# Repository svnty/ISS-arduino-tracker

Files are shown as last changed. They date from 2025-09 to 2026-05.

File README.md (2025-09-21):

<p align="center">
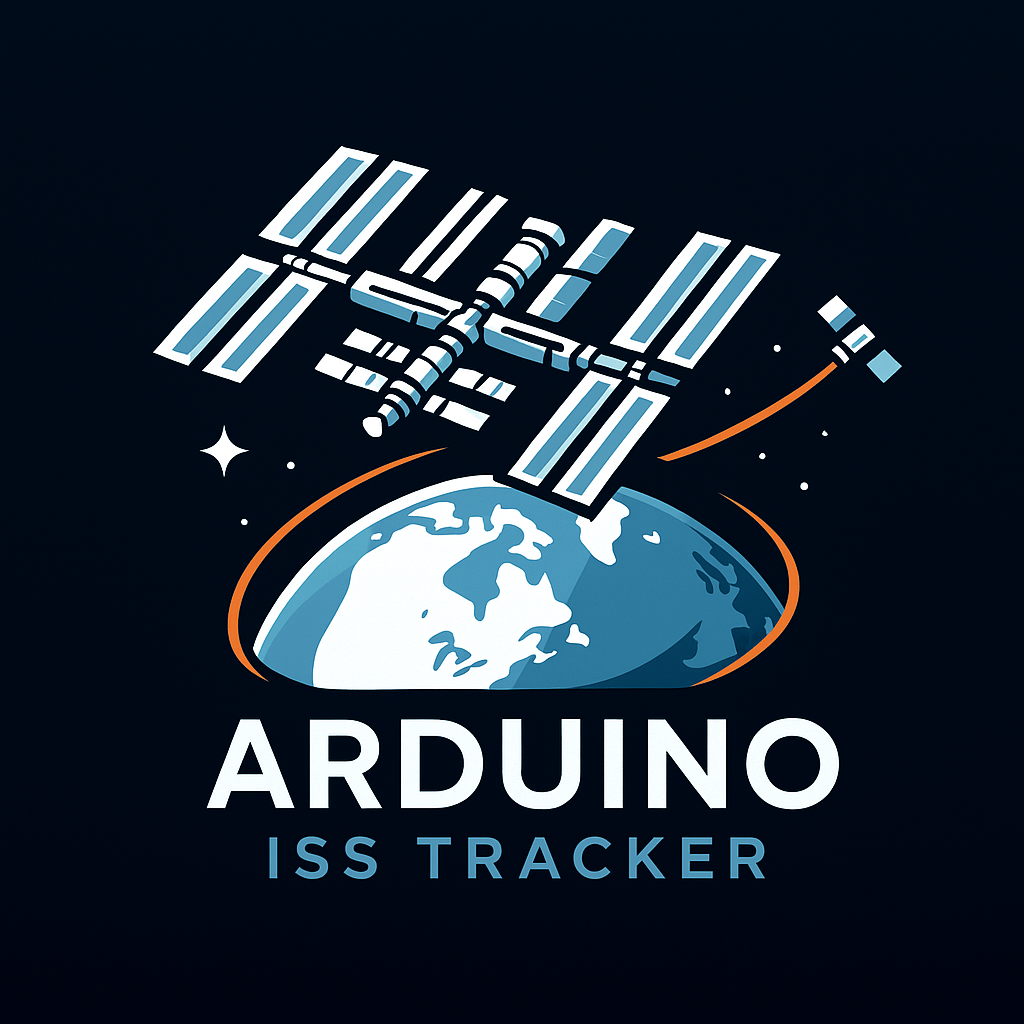
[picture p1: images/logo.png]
  
</p>

# International Space Station Orbit Tracker

Arduino implementation of an ISS tracker

Print all files in stl_files folder, use Nylon for the bearing (Race Inner Bottom, Race Inner Top, Race Outer, Rolls) at a high infill, and PLA for everything else at 15% infill.

## Model

<p align="center">
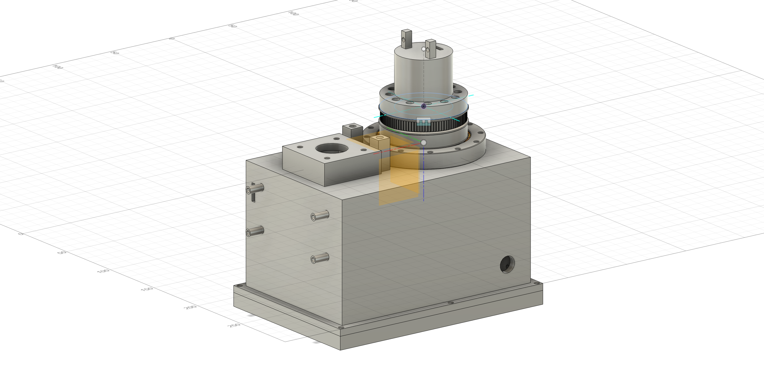
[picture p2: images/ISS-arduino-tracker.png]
International Space Station Orbit Tracker
  
</p>

## Parts list

| Part | Cost (AUD) |
|--|--|
| [Ardino uno R4 WiFi](https://www.jaycar.com.au/arduino-uno-wifi-r4-development-board/p/XC9211) | $50 |
| [Nema 17 stepper motor](https://www.jaycar.com.au/nema17-stepper-motor/p/YM2756) | $25 |
| [SG90 servo motor](https://www.jaycar.com.au/arduino-compatible-9g-micro-servo-motor/p/YM2758) | $12 |
| [TMC2209 stepper motor driver](https://www.ebay.com.au/sch/i.html?_nkw=TMC2209) | $15 |
| [230V AC -> 12V DC power supply](https://www.jaycar.com.au/mean-well-35w-12v-3a-power-supply/p/MP3285) | $40 |
| [12V DC -> 9V DC voltage regulator](https://core-electronics.com.au/20w-adjustable-dc-dc-buck-converter-with-digital-display.html) | $10 |
| [GY-271 QMC5883 magnometer](https://www.ebay.com.au/sch/i.html?_nkw=QMC5883+GY-271) | $5 |
| [12 wire 5A slip ring 22mm](https://www.ebay.com.au/sch/i.html?_nkw=22mm+12+wire+5A+slip+ring) | $30 |
| 15 AWG wire | $5 |
| 20 AWG wire | $15 |
| Dupont jumper wires | $20 |
| 16x2 LCD + i2c Backpack | $10 |
| 1kg Nylon filament | $60 |
| 1kg PLA filament | $20 |
| [ATGM336H GPS](https://www.ebay.com.au/sch/i.html?_nkw=BDS+GPS+ATGM336H) | $20 |
| Solder breadboard | $15 |
| 3 pin rocker power switch | $10 |
| M3 nuts + screws | $10 |
| PTFE grease | $10 |
| Solder | $5 |
| Heat shrink | $5 |
| Electrical tape | $5 |
| 1m GT2 pulley belt | $10 |
| Superglue | $1 |
| 2.1mm DC barrel jack | $2 |
| Contact Cement | $10 |
| 100 uF capacitor | $2 |

Total cost: ≈ $400

## Tools used

1. Anycubic Kobra S1 3D printer
2. TS80 soldering iron
3. Phillips head screwdriver
4. Precision knife

# Build Example

<p align="center">
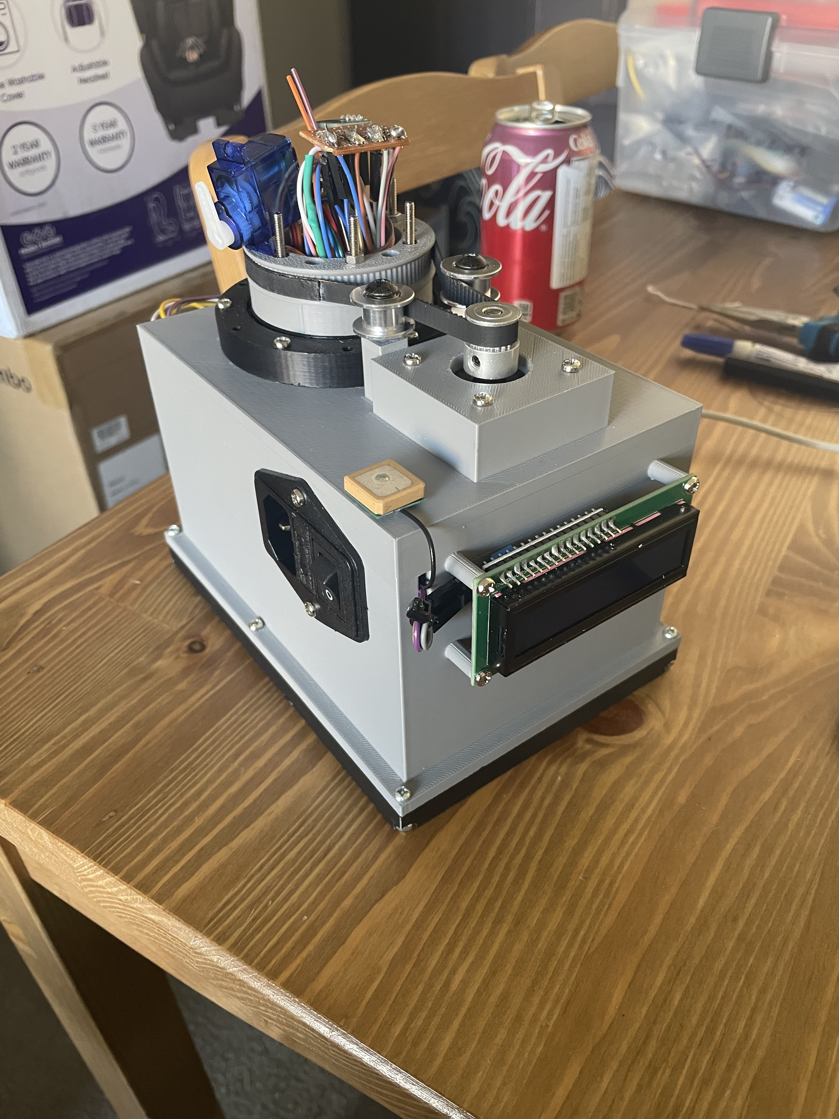
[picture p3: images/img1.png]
  
</p>

<p align="center">
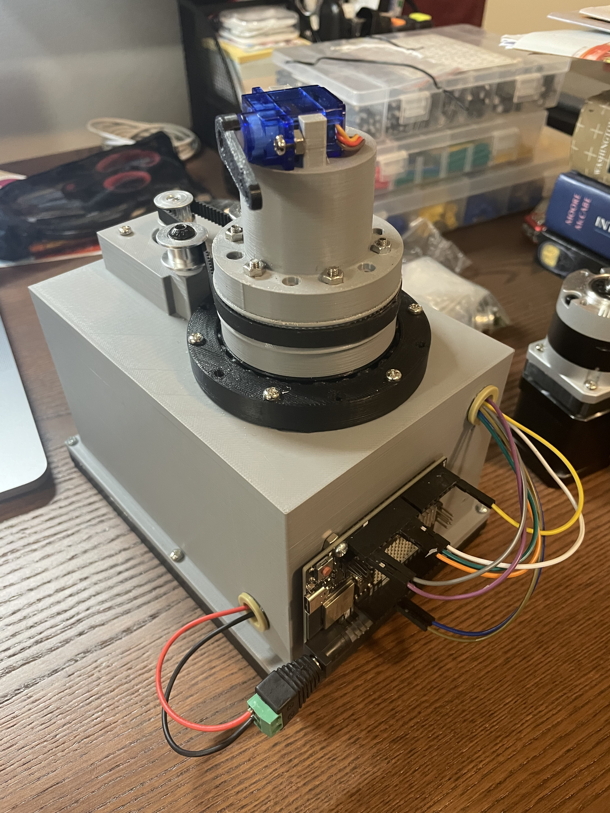
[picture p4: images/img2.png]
  
</p>

# Credits

Inspired by 
[Grady Hillhouse's ISS tracking pointer](https://github.com/gradyh/ISS-Tracking-Pointer/tree/master), as seen on [Youtube](https://www.youtube.com/watch?v=sIE0mcOGnms).

# Troubleshooting

Can't open the project? Open it in VS-Code and install the `svnty.vscode-arduino-intellisense` VS-Code extension.

# Power usage

Device uses 12W (aprox 0.23A).

# TODO

- Add 3S LiPo support?

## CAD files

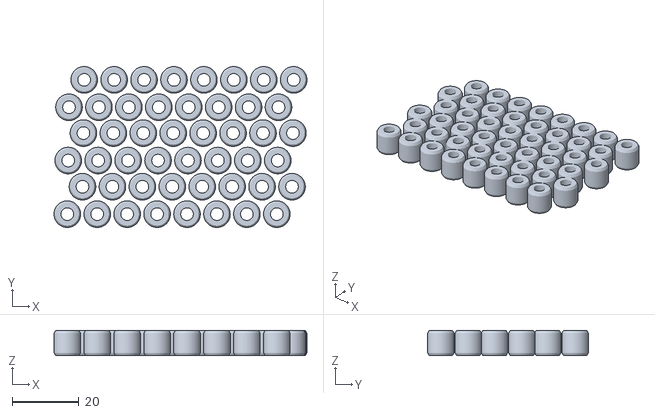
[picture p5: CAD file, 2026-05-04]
3d-models/stl_files/Rolls.stl
76.1 x 48.4 x 7.60

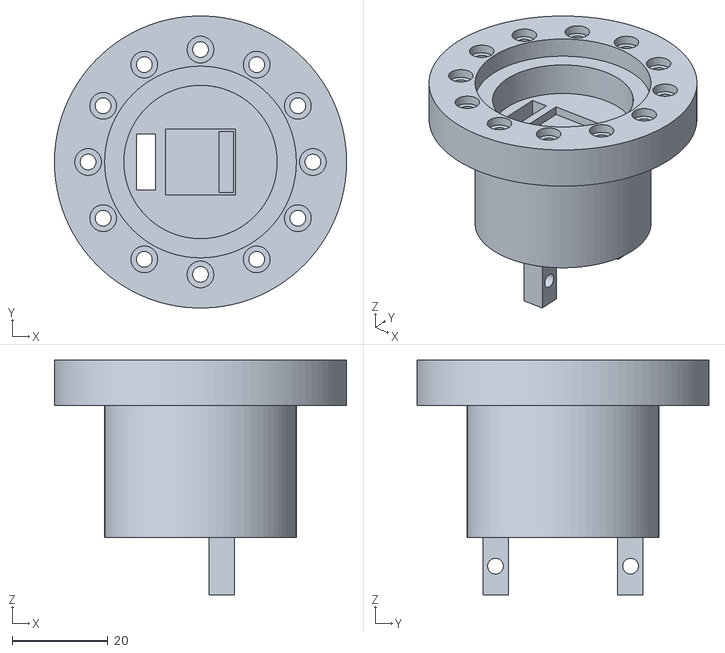
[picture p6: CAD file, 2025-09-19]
3d-models/stl_files/Top.stl
61.0 x 60.9 x 49.0

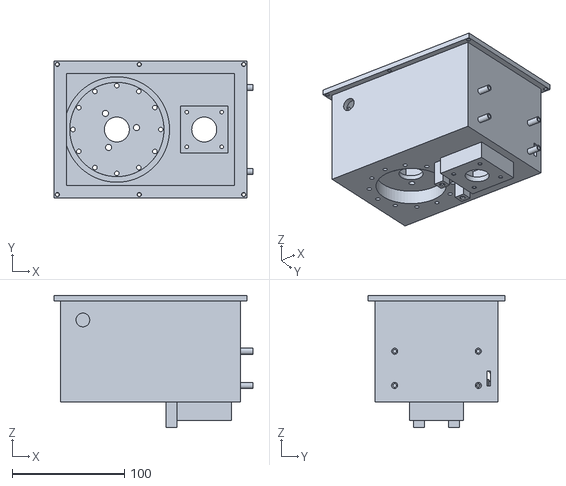
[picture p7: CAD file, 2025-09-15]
3d-models/stl_files/Housing.stl
177.3 x 122.0 x 117.8

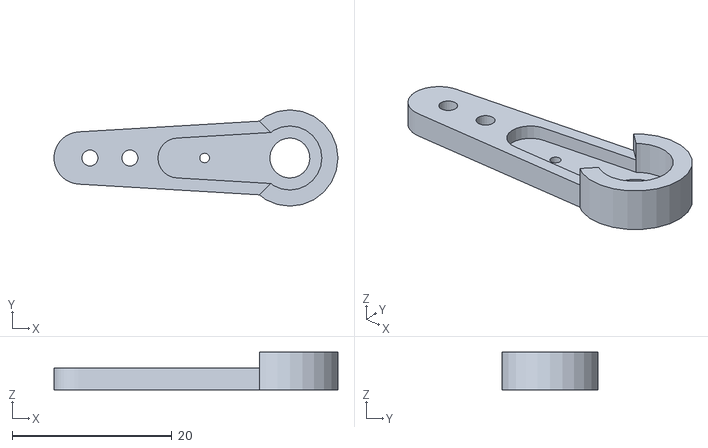
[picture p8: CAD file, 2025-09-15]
3d-models/stl_files/Servo-Extender.stl
35.5 x 12.0 x 4.70

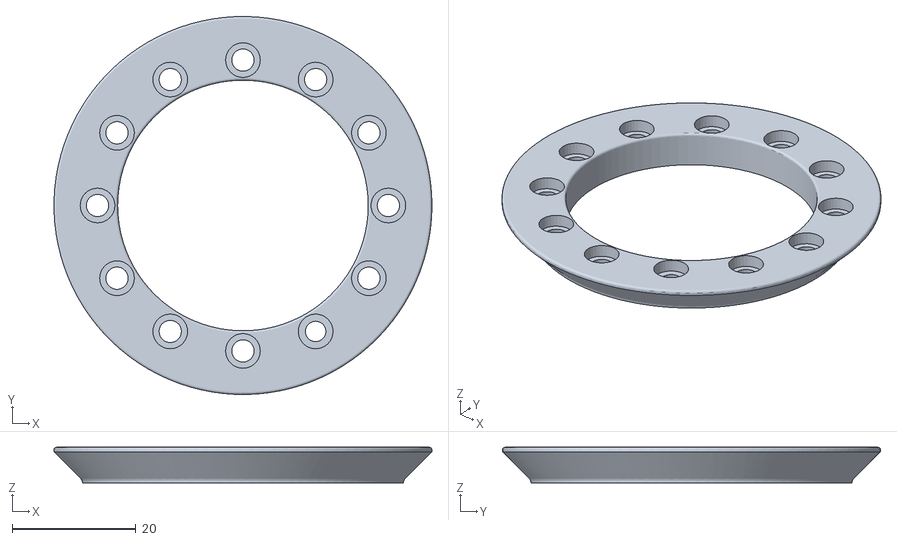
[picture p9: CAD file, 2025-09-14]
3d-models/stl_files/Race Inner Top.stl
61.0 x 61.0 x 5.73

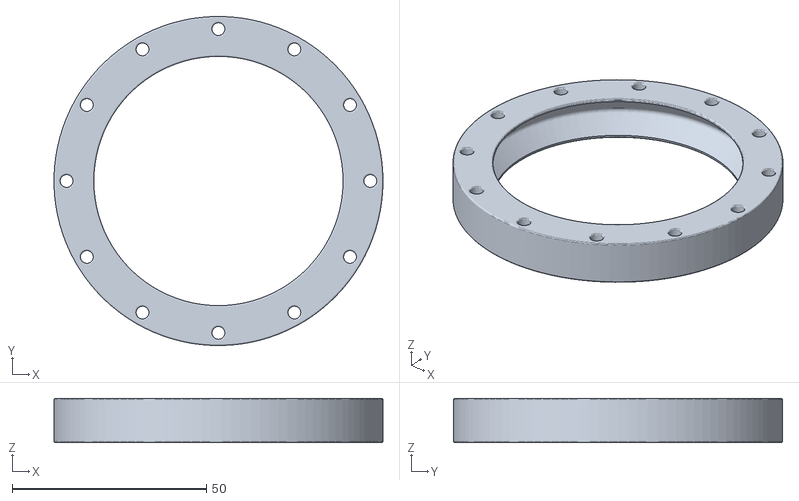
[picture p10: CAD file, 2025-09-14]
3d-models/stl_files/Race Outer.stl
84.7 x 84.7 x 11.5

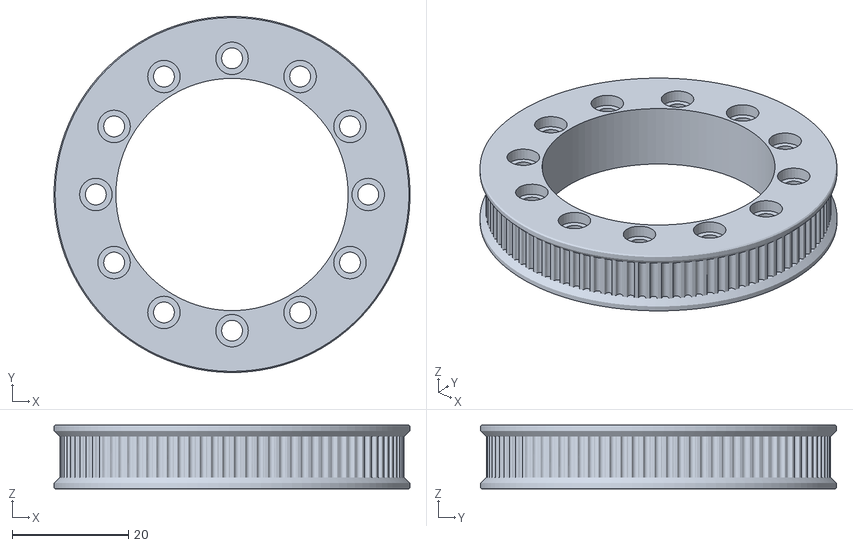
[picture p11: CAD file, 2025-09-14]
3d-models/stl_files/Pulley.stl
61.3 x 61.3 x 11.0

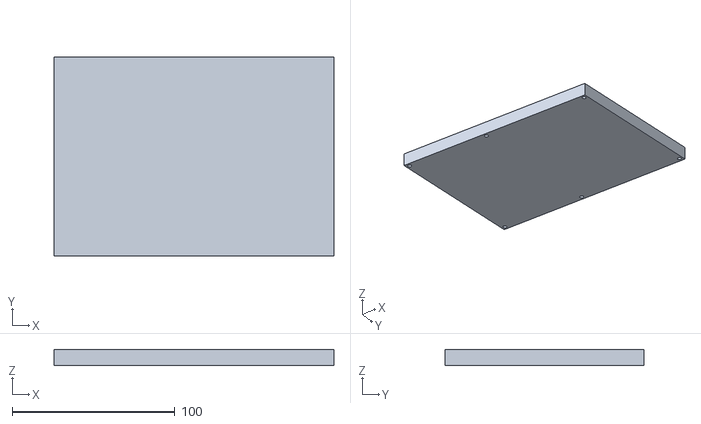
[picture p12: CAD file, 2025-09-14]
3d-models/stl_files/Base.stl
172.0 x 122.0 x 10.0

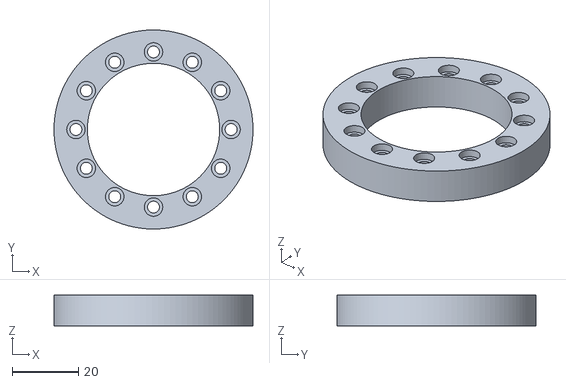
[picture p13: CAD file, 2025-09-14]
3d-models/stl_files/Spacer.stl
60.2 x 60.2 x 9.30

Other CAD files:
3d-models/stl_files/Race Inner Bottom.stl
3d-models/fusion-360/ISS-arduino-tracker.f3d

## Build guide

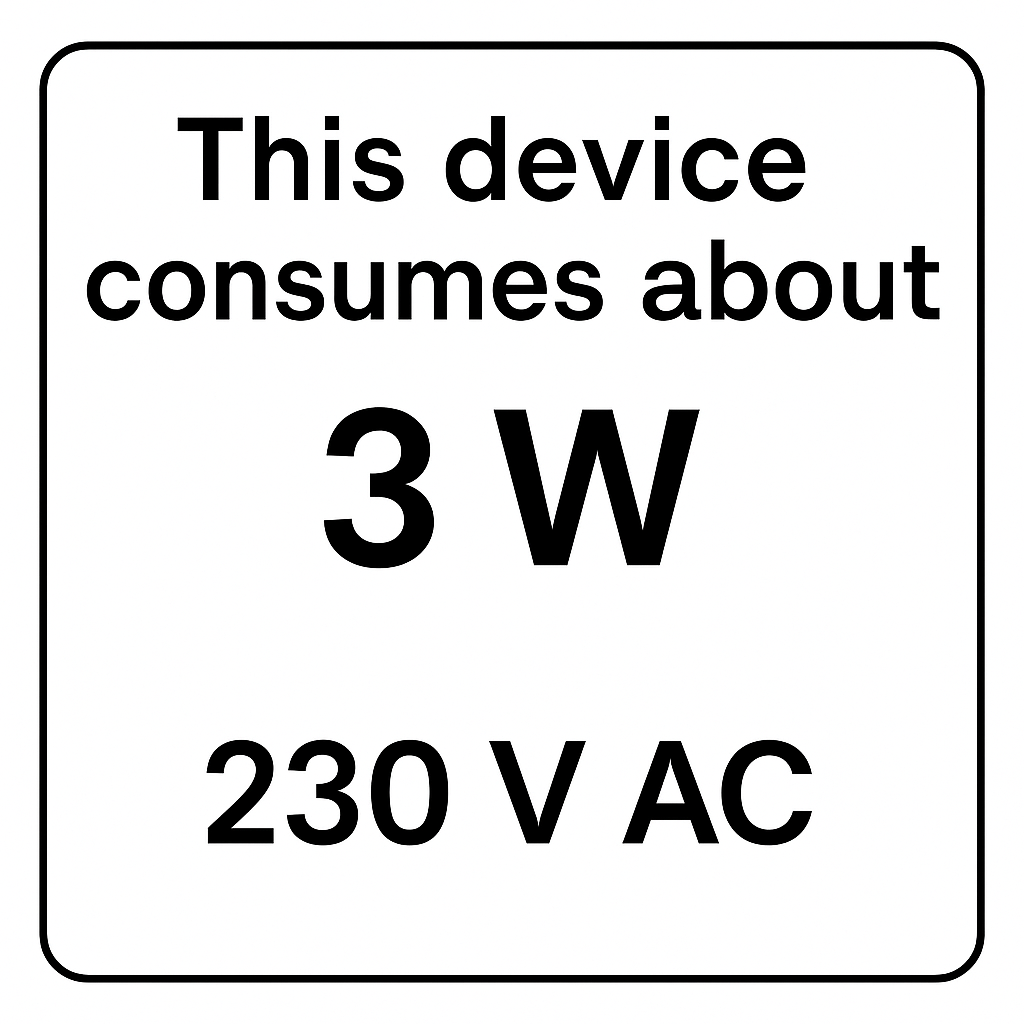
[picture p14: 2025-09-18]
images/power-usage.png

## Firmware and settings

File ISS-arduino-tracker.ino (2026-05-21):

/**
 * International Space Station (ISS) orbit tracker
 * Tracks the ISS using TLE data from Celestrak, observer location from GPS,
 * magnetic declination from NOAA, and points a motorized antenna mount
 * towards the ISS.
 *
 * @author svnty (Jake Walklate)
 * @date September 2025
 * @copyright © 2025 Jake Walklate
 */

#include <Arduino.h>
#include <ArduinoJson.h>
#include <LiquidCrystal_I2C.h>
#include <QMC5883LCompass.h>
#include <Servo.h>
#include <TinyGPSPlus.h>
#include <WiFiS3.h>
#include <Wire.h>
#include <math.h>

#include "SGP4_vallado/sgp4coord.cpp"
#include "SGP4_vallado/sgp4coord.h"
#include "SGP4_vallado/sgp4ext.cpp"
#include "SGP4_vallado/sgp4ext.h"
#include "SGP4_vallado/sgp4unit.cpp"
#include "SGP4_vallado/sgp4unit.h"

// -------- SYSTEM TOGGLES --------
static const bool ENABLE_WIFI = true;
static const bool ENABLE_LOG = true;
static const bool ENABLE_GPS = true;

// -------- CONSTANTS --------
// pins
static const uint8_t ELEVATION_PIN = 9;
static const uint8_t AZIMUTH_DIR_PIN = 10;
static const uint8_t AZIMUTH_STEP_PIN = 11;
static const uint8_t GPS_RX_PIN = 12;
// stepper motor
static const float TMC2209_RESISTANCE = 0.11;  // ohms
// wifi
static const char *WIFI_SSID = "Jakes iPhone", *WIFI_PASSWORD = "izeh5zemxa05r";
// http
static const char *DECLINATION_HOST = "www.ngdc.noaa.gov";
static const char *DECLINATION_API_KEY = "zNEw7";
static const char *TLE_API_HOST = "celestrak.org";
static const uint16_t PORT = 443;
// i2c
static const uint8_t MAX_i2c_DEVICES = 16;
// compass
static const float COMPASS_AZIMUTH_OFFSET = 17.0;               // degrees
static const float COMPASS_JUMP_THRESHOLD = 5.0;               // degrees
static const unsigned long COMPASS_CHECK_INTERVAL = 5 * 1000;  // 5 seconds
// lcd
static const unsigned long LCD_UPDATE_INTERVAL = 5 * 1000;  // 5 seconds
// wifi
static const unsigned long WIFI_UPDATE_INTERVAL = 60 * 60 * 1000 + 60 * 30 * 1000;  // 1 hour + 30 minutes
static const unsigned long WIFI_TIMEOUT_TIME = 60 * 1000;          // 1 minute
// gps
static const unsigned long GPS_UPDATE_INTERVAL = 10 * 60 * 1000;  // 10 minutes
static const unsigned long GPS_TIMEOUT_INTERVAL = 60 * 1000;      // 1 minute

// -------- VARIABLES --------
// timers
static unsigned long lastLcdUpdateTime = 0;
static unsigned long lastLcdResetTime = 0;
static unsigned long lastGpsUpdateTime = 0;
static unsigned long lastWiFiUpdateTime = 0;
static unsigned long lastWiFiReconnectAttemptTime = 0;
static unsigned long gpsTimeoutTimer = 0;
static unsigned long lastTimeUpdateMillis = 0;
// http data
static bool foundISSbyWifi = false;
static uint8_t findISSbyWifiAttempts = 0;
static bool foundDeclinationByWifi = false;
static uint8_t findDeclinationByWifiAttempts = 0;
static float magneticDeclination = 12.7;  // degrees
static char tle_line1[70];
static char tle_line2[70];
// gps data
static double observerLatitude = 0.0, observerLongitude = 0.0, observerAltitude = 0.0;
static int year, month, day, hour, minute, second;
static bool isGpsFixed = false;
static uint32_t gpsDateAge = 0;
static uint32_t gpsLocationAge = 0;
// motor control
static float currentAzimuth = 0.0;
static float currentElevation = 95.0;
// compass
static float previousCompassHeading = 0.0;
static unsigned long lastCompassCheckTime = 0;
static unsigned long compassLastCalibrate = 0;
static float compassOffsetX = 0.0, compassOffsetY = 0.0, compassOffsetZ = 0.0;
static float compassScaleX = 1.0, compassScaleY = 1.0, compassScaleZ = 1.0;
// i2c
static uint8_t i2cDeviceAddresses[MAX_i2c_DEVICES];
static uint8_t i2cDeviceCount = 0;
// lcd
static unsigned long lcdDisplayMode = 0;

// -------- SERIALS --------
HardwareSerial &GPS_SERIAL = Serial1;

// -------- OBJECTS --------
TinyGPSPlus gps;
LiquidCrystal_I2C lcd(0x27, 16, 2);
QMC5883LCompass compass;
elsetrec satrec;
Servo elevation;

// -------- FUNCTIONS --------
void calibrateCompass() {
  int minX = 32767, maxX = -32768;
  int minY = 32767, maxY = -32768;
  int minZ = 32767, maxZ = -32768;

  Serial.println("Starting QMC5883L calibration. Please rotate the sensor in all directions for 20 seconds.");
  unsigned long startTime = millis();
  while (millis() - startTime < 20 * 1000) {
    compass.read();

    int x = compass.getX();
    int y = compass.getY();
    int z = compass.getZ();
    minX = min(minX, x); maxX = max(maxX, x);
    minY = min(minY, y); maxY = max(maxY, y);
    minZ = min(minZ, z); maxZ = max(maxZ, z);

    digitalWrite(AZIMUTH_STEP_PIN, HIGH);
    delayMicroseconds(1000);
    digitalWrite(AZIMUTH_STEP_PIN, LOW);
    delayMicroseconds(1000);
  }

  compassOffsetX = (maxX + minX) / 2.0;
  compassOffsetY = (maxY + minY) / 2.0;
  compassOffsetZ = (maxZ + minZ) / 2.0;
  compassScaleX = (maxX - minX) / 2.0;
  compassScaleY = (maxY - minY) / 2.0;
  compassScaleZ = (maxZ - minZ) / 2.0;

  Serial.println("Compass calibration complete.");
  Serial.print("Offset X: "); Serial.println(compassOffsetX);
  Serial.print("Offset Y: "); Serial.println(compassOffsetY);
  Serial.print("Offset Z: "); Serial.println(compassOffsetZ);
  Serial.print("Scale X: "); Serial.println(compassScaleX);
  Serial.print("Scale Y: "); Serial.println(compassScaleY);
  Serial.print("Scale Z: "); Serial.println(compassScaleZ);
  lcdSetSecondLine("OK");
}

void lcdClear() {
  lcd.setCursor(0, 0);
  lcd.print("                ");
  lcd.setCursor(0, 1);
  lcd.print("                ");
}

void lcdSetFirstLine(String firstLineText) {
  lcd.setCursor(0, 0);
  lcd.print("                ");
  lcd.setCursor(0, 0);
  lcd.print(firstLineText);
}

void lcdSetSecondLine(String secondLineText) {
  lcd.setCursor(0, 1);
  lcd.print("                ");
  lcd.setCursor(0, 1);
  lcd.print(secondLineText);
}

void updateLCD(double azimuth_deg, double elevation_deg, double range_km) {
  // reset the LCD every 2 minutes to prevent it from printing garbage
  if (millis() - lastLcdResetTime >= 2 * 60 * 1000) {
    lcd.begin(16, 2);
    lastLcdResetTime = millis();
  }
  lcdClear();

  // If ISS is overhead (elevation > 10°), always show ISS position
  bool issOverhead = elevation_deg > 10.0;

  if (issOverhead) {
    lcdSetFirstLine("ISS VISIBLE!");
    char buffer[17];
    snprintf(buffer, sizeof(buffer), "Az:%03.0f El:%02.0f", azimuth_deg, elevation_deg);
    lcdSetSecondLine(buffer);
    return;
  }

  // If ISS is visible but not overhead, show ISS info
  if (elevation_deg > 0) {
    lcdSetFirstLine("ISS UPWARDS");
    char buffer[17];
    snprintf(buffer, sizeof(buffer), "Az:%03.0f El:%02.0f", azimuth_deg, elevation_deg);
    lcdSetSecondLine(buffer);
    return;
  }

  unsigned long modeTime = (millis() / LCD_UPDATE_INTERVAL) % 7;

  switch (modeTime) {
    case 0:  // ISS status and range
      lcdSetFirstLine("ISS DISTANCE");
      {
        char buffer[17];
        snprintf(buffer, sizeof(buffer), "%03.0f km", range_km);
        lcdSetSecondLine(buffer);
      }
      break;
    case 1:  // Observer location
      lcdSetFirstLine("OBSERVER LOCATION");
      {
        char buffer[17];
        snprintf(buffer, sizeof(buffer), "%.2f,%.2f", observerLatitude, observerLongitude);
        lcdSetSecondLine(buffer);
      }
      break;
    case 2:  // Current time
      lcdSetFirstLine("UTC TIME (24 HR)");
      {
        char buffer[17];
        snprintf(buffer, sizeof(buffer), "%02d:%02d %d/%d/%02d", hour, minute, day, month, (year % 100));
        lcdSetSecondLine(buffer);
      }
      break;
    case 3:  // Compass heading and motor position
      lcdSetFirstLine("COMPASS/MOTOR");
      {
        char buffer[17];
        float compassHeading = getCompassHeading();
        snprintf(buffer, sizeof(buffer), "C:%05.1f M:%05.1f", compassHeading, currentAzimuth);
        lcdSetSecondLine(buffer);
      }
      break;
    case 4:  // ISS current azimuth (even when below horizon)
      lcdSetFirstLine("ISS DIRECTION");
      {
        char buffer[17];
        snprintf(buffer, sizeof(buffer), "Az:%03.0f E:%0.0fkm", azimuth_deg, elevation_deg);
        lcdSetSecondLine(buffer);
      }
      break;
    case 5:
      lcdSetFirstLine("ISS");
      lcdSetSecondLine("BELOW HORIZON");
      break;
    case 6:
      if (isGpsFixed) {
        lcdSetFirstLine("GPS ACCURATE");
      } else {
        lcdSetFirstLine("GPS ERROR");
      }
      if (foundISSbyWifi) {
        lcdSetSecondLine("ISS ACCURATE");
      } else {
        lcdSetSecondLine("ISS DATA ERROR");
      }
      break;
  }
}

void makeTleApiRequest() {
  Serial.println("Making HTTPS API request...");

  WiFiSSLClient client;

  Serial.print("Connecting to ");
  Serial.print(TLE_API_HOST);
  Serial.print(":");
  Serial.println(PORT);

  if (!client.connect(TLE_API_HOST, PORT)) {
    Serial.println("Connection to server failed!");
    lcdSetSecondLine("TLE ERROR");
    delay(2000);
    return;
  }

  Serial.println("Connected to server");

  String request = "GET " + String("/NORAD/elements/gp.php?GROUP=stations&FORMAT=tle") + " HTTP/1.1\r\n";
  request += "Host: " + String(TLE_API_HOST) + "\r\n";
  request += "User-Agent: ArduinoUnoR4Wifi/1.0\r\n";
  request += "Cache-Control: no-cache\r\n";
  request += "Connection: close\r\n";
  request += "\r\n";

  client.print(request);
  Serial.println("Request sent");
  Serial.println("Request details:");
  Serial.println(request);

  String httpResponse = "";
  bool headersEnded = false;
  unsigned long timeout = millis();
  const unsigned long timeoutLimit = 10000;  // 10 second timeout

  while ((client.connected() || client.available()) && (millis() - timeout < timeoutLimit)) {
    if (client.available()) {
      String line = client.readStringUntil('\n');

      if (!headersEnded) {
        Serial.println("Header: " + line);

        // Check for end of headers (empty line)
        if (line.length() <= 1) {
          headersEnded = true;
          Serial.println("--- End of Headers ---");
          Serial.println("Reading response body...");
        }
      } else {
        // We're in the body now
        httpResponse += line;
      }

      // Reset timeout when data is received
      timeout = millis();
    }
    delay(1);
  }

  client.stop();
  Serial.println("Connection closed");

  int issIndex = httpResponse.indexOf("ISS (ZARYA)");
  if (httpResponse.isEmpty() == false && issIndex >= 0) {
    foundISSbyWifi = true;
    Serial.println(httpResponse);
    parseTLEData(httpResponse, issIndex);
    lcdSetSecondLine("OK");
  } else {
    foundISSbyWifi = false;
  }

  if (!foundISSbyWifi) {
    Serial.println("No valid TLE data received!");
    return;
  }
}

void parseTLEData(String data, int issIndex) {
  Serial.println("Parsing TLE data...");

  // Find the first TLE line (starts with "1 25544")
  int line1Index = data.indexOf("1 25544", issIndex);
  if (line1Index == -1) {
    Serial.println("TLE Line 1 not found!");
    return;
  }

  // Find the second TLE line (starts with "2 25544")
  int line2Index = data.indexOf("2 25544", line1Index);
  if (line2Index == -1) {
    Serial.println("TLE Line 2 not found!");
    return;
  }

  Serial.println("Found ISS (ZARYA) data!");

  // Extract Line 1 (69 characters for standard TLE format)
  String line1 = data.substring(line1Index, line1Index + 69);
  line1.trim();

  // Extract Line 2 (69 characters for standard TLE format)
  String line2 = data.substring(line2Index, line2Index + 69);
  line2.trim();

  // Copy to global variables
  strcpy(tle_line1, line1.c_str());
  strcpy(tle_line2, line2.c_str());

  Serial.println("TLE Line 1: " + line1);
  Serial.println("TLE Line 2: " + line2);
  Serial.println("TLE data parsed successfully!");
  lcdSetSecondLine("TLE OK");
}

void makeDeclinationApiRequest() {
  Serial.println("Making HTTPS API request...");

  WiFiSSLClient client;

  Serial.print("Connecting to ");
  Serial.print(DECLINATION_HOST);
  Serial.print(":");
  Serial.println(PORT);

  if (!client.connect(DECLINATION_HOST, PORT)) {
    Serial.println("Connection to server failed!");
    lcdSetSecondLine("DECLINATION ERROR");
    delay(2000);
    return;
  }

  Serial.println("Connected to server");

  char apiPath[256];
  snprintf(apiPath, sizeof(apiPath), "/geomag-web/calculators/calculateDeclination?lat1=%.6f&lon1=%.6f&key=%s&resultFormat=json", observerLatitude, observerLongitude, DECLINATION_API_KEY);

  String request = "GET " + String(apiPath) + " HTTP/1.1\r\n";
  request += "Host: " + String(DECLINATION_HOST) + "\r\n";
  request += "User-Agent: ArduinoUnoR4Wifi/1.0\r\n";
  request += "Accept: application/json\r\n";
  request += "Cache-Control: no-cache\r\n";
  request += "Connection: close\r\n";
  request += "\r\n";

  client.print(request);
  Serial.println("Request sent");
  Serial.println("Request details:");
  Serial.println(request);

  String jsonResponse = "";
  bool headersEnded = false;
  unsigned long timeout = millis();
  const unsigned long timeoutLimit = 10000;

  while ((client.connected() || client.available()) && (millis() - timeout < timeoutLimit)) {
    if (client.available()) {
      String line = client.readStringUntil('\n');

      if (!headersEnded) {
        Serial.println("Header: " + line);

        // Check for end of headers (empty line)
        if (line.length() <= 1) {
          headersEnded = true;
          Serial.println("--- End of Headers ---");
          Serial.println("Reading response body...");
        }
      } else {
        jsonResponse += line;
      }

      // Reset timeout when data is received
      timeout = millis();
    }
    delay(1);
  }

  client.stop();
  Serial.println("Connection closed");

  if (jsonResponse.length() == 0) {
    Serial.println("No response body received!");
    return;
  } else {
    // assuming the data is valid if we got something
    // todo: improve this check
    foundDeclinationByWifi = true;
  }

  parseDeclinationJsonResponse(jsonResponse);
}

String cleanDeclinationChunkedJSON(String rawJson) {
  int jsonStart = rawJson.indexOf('{');

  int jsonEnd = rawJson.lastIndexOf('}');

  if (jsonStart >= 0 && jsonEnd > jsonStart) {
    String cleanJson = rawJson.substring(jsonStart, jsonEnd + 1);
    Serial.println("Cleaned JSON extracted successfully");
    return cleanJson;
  } else {
    Serial.println("Could not find JSON boundaries!");
    return rawJson;
  }
}

void parseDeclinationJsonResponse(String jsonString) {
  Serial.println("Parsing JSON response...");
  Serial.println("Raw JSON:");
  Serial.println(jsonString);
  Serial.println("JSON length: " + String(jsonString.length()));

  String cleanedJson = cleanDeclinationChunkedJSON(jsonString);
  Serial.println("Using cleaned JSON:");
  Serial.println(cleanedJson);

  JsonDocument doc;

  DeserializationError error = deserializeJson(doc, cleanedJson);

  if (error) {
    Serial.print("JSON parsing failed: ");
    Serial.println(error.c_str());
    Serial.println("Attempting to debug JSON structure...");
    Serial.println("First 50 chars: " + cleanedJson.substring(0, 50));
    return;
  }

  Serial.println("JSON parsed successfully!");

  // Parse the NOAA geomagnetic data
  if (doc["result"].is<JsonArray>()) {
    JsonArray results = doc["result"];
    if (results.size() > 0) {
      JsonObject result = results[0];

      if (!result["declination"].isNull()) {
        magneticDeclination = result["declination"];
        foundDeclinationByWifi = true;
        lcdSetSecondLine("DECLINATION OK");
        Serial.print("Magnetic Declination: ");
        Serial.print(magneticDeclination, 5);
        Serial.println("°");
      }
    }
  } else {
    Serial.println("Unexpected JSON structure: 'result' is not an array");
  }
}
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
void loop() {
  i2cBusCheck();
  updateLocalTime();
  
  // update GPS data every hour
  if (ENABLE_GPS) {
    if (millis() - lastGpsUpdateTime >= GPS_UPDATE_INTERVAL) {
      lcdClear();
      lcdSetFirstLine("UPDATING GPS");
      updateGPSData();
    }
  }

  // update the TLE and declination every hour
  if (ENABLE_WIFI) {
    if (millis() - lastWiFiUpdateTime >= WIFI_UPDATE_INTERVAL) {
      lcdClear();
      lcdSetFirstLine("UPDATING TLE");
      if (WiFi.status() != WL_CONNECTED) {
        connectToWiFi();
      }
      if (WiFi.status() == WL_CONNECTED) {
        makeTleApiRequest();
        makeDeclinationApiRequest();
      }
      lastWiFiUpdateTime = millis();
    }
  }

  // Check for compass jumps indicating the tracker was moved
  if (checkForCompassJump()) {
    recalibrateAzimuth();
  }

  double jdnow;
  jday(year, month, day, hour, minute, second, jdnow);

  if (ENABLE_LOG) {
    Serial.println("==================");
    Serial.print("Current time: ");
    Serial.print(year);
    Serial.print("/");
    Serial.print(month);
    Serial.print("/");
    Serial.print(day);
    Serial.print(" ");
    Serial.print(hour);
    Serial.print(":");
    Serial.print(minute);
    Serial.print(":");
    Serial.println(second);
    Serial.print("Julian day now: ");
    Serial.println(jdnow, 8);
    Serial.print("Satellite epoch JD: ");
    Serial.println(satrec.jdsatepoch, 8);
    Serial.print("TLE Line 1: ");
    Serial.println(tle_line1);
    Serial.print("TLE Line 2: ");
    Serial.println(tle_line2);
  }

  double tsince = (jdnow - satrec.jdsatepoch) * 24.0 * 60.0;

  if (ENABLE_LOG) {
    Serial.print("Time since epoch (minutes): ");
    Serial.println(tsince, 2);
  }

  double ro[3], vo[3];
  sgp4(wgs72, satrec, tsince, ro, vo);

  if (satrec.error != 0) {
    lcdSetFirstLine("SGP4 ERROR");
    lcdSetSecondLine(String(satrec.error));
    Serial.print("SGP4 Error: ");
    Serial.println(satrec.error);
    delay(1000);
    return;
  }

  if (ENABLE_LOG) {
    Serial.print("SGP4 position (km): ");
    Serial.print(ro[0], 3);
    Serial.print(", ");
    Serial.print(ro[1], 3);
    Serial.print(", ");
    Serial.println(ro[2], 3);

    // Convert ISS TEME position to lat/lon for comparison
    double issLatLonAlt[3];
    double recef[3], vecef[3];
    teme2ecef(ro, vo, jdnow, recef, vecef);
    ijk2ll(recef, issLatLonAlt);

    Serial.print("ISS calculated lat: ");
    Serial.println(degrees(issLatLonAlt[0]), 6);
    Serial.print("ISS calculated lon: ");
    Serial.println(degrees(issLatLonAlt[1]), 6);
    Serial.print("ISS calculated alt (km): ");
    Serial.println(issLatLonAlt[2], 3);
  }

  double razel[3], razelrates[3];

  if (ENABLE_LOG) {
    Serial.print("Observer lat (deg): ");
    Serial.println(observerLatitude, 6);
    Serial.print("Observer lon (deg): ");
    Serial.println(observerLongitude, 6);
    Serial.print("Observer alt (km): ");
    Serial.println(observerAltitude, 6);
    Serial.print("Observer lat (rad): ");
    Serial.println(radians(observerLatitude), 6);
    Serial.print("Observer lon (rad): ");
    Serial.println(radians(observerLongitude), 6);
  }

  rv2azel(ro, vo, radians(observerLatitude), radians(observerLongitude), observerAltitude, jdnow, razel, razelrates);

  if (ENABLE_LOG) {
    Serial.print("Raw razel: ");
    Serial.print(razel[0], 3);
    Serial.print(" km, ");
    Serial.print(degrees(razel[1]), 3);
    Serial.print("° az, ");
    Serial.print(degrees(razel[2]), 3);
    Serial.println("° el");
  }

  double azimuth_deg = degrees(razel[1]);
  double elevation_deg = degrees(razel[2]);
  double range_km = razel[0];
  if (azimuth_deg < 0) {
    azimuth_deg += 360.0;
  }

  // Test with actual SGP4 ISS position instead of hardcoded coordinates
  if (ENABLE_LOG) {
    // Get ISS lat/lon from SGP4 for manual calculation
    double issLatLonAlt[3];
    double recef[3], vecef[3];
    teme2ecef(ro, vo, jdnow, recef, vecef);
    ijk2ll(recef, issLatLonAlt);

    double issLatDeg = degrees(issLatLonAlt[0]);
    double issLonDeg = degrees(issLatLonAlt[1]);

    testAzimuthCalculation(issLatDeg, issLonDeg);
  }

  if (ENABLE_LOG) {
    Serial.print("FINAL: Azimuth: ");
    Serial.print(azimuth_deg, 2);
    Serial.print("° (");
    // Add cardinal direction interpretation
    if (azimuth_deg >= 337.5 || azimuth_deg < 22.5)
      Serial.print("N");
    else if (azimuth_deg >= 22.5 && azimuth_deg < 67.5)
      Serial.print("NE");
    else if (azimuth_deg >= 67.5 && azimuth_deg < 112.5)
      Serial.print("E");
    else if (azimuth_deg >= 112.5 && azimuth_deg < 157.5)
      Serial.print("SE");
    else if (azimuth_deg >= 157.5 && azimuth_deg < 202.5)
      Serial.print("S");
    else if (azimuth_deg >= 202.5 && azimuth_deg < 247.5)
      Serial.print("SW");
    else if (azimuth_deg >= 247.5 && azimuth_deg < 292.5)
      Serial.print("W");
    else if (azimuth_deg >= 292.5 && azimuth_deg < 337.5)
      Serial.print("NW");
    Serial.print("), Elevation: ");
    Serial.print(elevation_deg, 2);

    // Add visibility status
    if (elevation_deg > 0) {
      Serial.print("° (VISIBLE)");
    } else {
      Serial.print("° (BELOW HORIZON - ISS NOT VISIBLE)");
    }

    Serial.print(", Range: ");
    Serial.print(range_km, 2);
    Serial.println(" km");

    // Add compass vs SGP4 comparison
    float currentCompass = getCompassHeading();
    Serial.print("Current compass heading: ");
    Serial.print(currentCompass, 2);
    Serial.print("° vs SGP4 azimuth: ");
    Serial.print(azimuth_deg, 2);
    Serial.print("° (diff: ");
    Serial.print(azimuth_deg - currentCompass, 2);
    Serial.println("°)");

    Serial.println("==================");
  }

  moveElevationTo((float)elevation_deg);
  moveAzimuthTo((float)azimuth_deg);

  // Update LCD less frequently to reduce I2C interference
  if (millis() - lastLcdUpdateTime >= LCD_UPDATE_INTERVAL) {
    updateLCD(azimuth_deg, elevation_deg, range_km);
    lastLcdUpdateTime = millis();
  }
}

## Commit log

2020-12-27 hall effect
2025-09-14 add STL files
    [Base.stl, Housing.stl, Pulley.stl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]
2025-09-15 finish housing
    [ISS-arduino-tracker v1.f3d, Servo-Extender.stl, Top.stl]
2025-09-15 move directory
    [Base.stl, Housing.stl, ISS-arduino-tracker v1.f3d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]
2025-09-15 fix stl
    [Housing.stl, ISS-arduino-tracker v1.f3d, ISS-arduino-tracker.f3d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]
2025-09-16 [ImgBot] Optimize images
    *Total -- 31,175.67kb -> 27,355.65kb (12.25%)
    /images/logo.png -- 1,209.49kb -> 942.07kb (22.11%)
    /images/ISS-arduino-tracker.png -- 658.37kb -> 577.92kb (12.22%)
    /images/img2.png -- 14,645.49kb -> 12,902.76kb (11.9%)
    /images/img1.png -- 14,662.32kb -> 12,932.90kb (11.79%)
2025-09-17 maybe a bug fix?
    [ISS-arduino-tracker.ino]
2025-09-17 bug-fix: slow stepper
2025-09-20 wire speed
2025-09-21 fix calculations in readme
    [ISS-arduino-tracker.ino]
2026-05-04 add robust UTC timing
    [Base.stl, Housing.stl, ISS-arduino-tracker.f3d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]
